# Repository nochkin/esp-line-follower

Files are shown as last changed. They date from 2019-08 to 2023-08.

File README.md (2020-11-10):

# esp-line-follower
## Purpose
The goal of the project is to teach beginners into robotics without fearing and over-complicated or expensive parts.
It's indended to be open enough for future experiments and improvements.

## Required skills
* Basic soldering skills.
  A few wires need to be soldered here and there, nothing major.
* Some understanding on how electronic components are connected together
  Just enough to know the difference between "+" and "-", signal and power lines, etc.
* Basic knowledge on Arduino IDE and how sketches are uploaded.

## Required parts
This is the minimum list of required parts. Basically, these are the parts which are being used in this project.
The list should not limit you in case if you wish to add some additional functionality or make other experiments based on that.
* Microcontroller board.
  The project uses ESP8266 NodeMCU board with CP2102. Sometimes that board is referenced as "ESP8266 NodeMCU v2 DevKit".
  There are some variations of ESP8266 NodeMCU board with CH340G chip, but these are too wide to fit into motor driver shield and so can't be used.
* Motor driver shield.
  The shield is based on L293DD chip. A single chip contains four half-bridges which can be connected as two full bridges to drive two motors.
* A pair of Reflective Infrared sensor boards.
  These are sometimes called "Obstacles avoiding infrared sensor board". Each board contains an infrared LED and infrared photodiode.
  There are a lot of variations of those boards. I highly recommend to pick those with a small adjustment, this way it can be adjusted according to the current lighting and surrounding contrast.
* 2WD Robot Chassis.
  Normally, the chassis comes with two motors with built-in reductors, 4*AA battery holder and enough screws and mounting hardware to put everything together. You will still need some additional mounting/screws to put your ESP8266, Motor shield and Infrared sensors.

## Bill Of Materials (BOM)
All prices are approximate and depend on the source where you purchase it. My recommended sources are eBay and AliExpress. You can also find it on Amazon, but it tends to be slightly more expensive. All prices are in USD.

Qnty | Part | Cost | Buy
-- | - | - | -
1 | ESP8266 NodeMCU (CP2102) | $5.00 | [eBay](https://www.ebay.com/itm/201542946669), [AliExpress](https://www.aliexpress.com/item/32716698412.html), [Amazon](https://www.amazon.com/ESP8266-microcontroller-NodeMCU-WiFi-CP2102/dp/B071WRD25D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)
1 | L293DD Motor Shield for ESP8266 NodeMCU | $2.50 | [eBay](https://www.ebay.com/itm/400999618519), [AliExpress](https://www.aliexpress.com/item/32870926299.html), [Amazon](https://www.amazon.com/BeediY-NodeMCU-ESP-12E-ESP8266-Control/dp/B07QVCMM5B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)
2 | Infrared sensors | $1.50 | [eBay](https://www.ebay.com/itm/132461910910), [AliExpress](https://www.aliexpress.com/item/32757950384.html), [Amazon](https://www.amazon.com/HiLetgo-Infrared-Avoidance-Reflective-Photoelectric/dp/B07W97H2WS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)
1 | 2WD Robot Chassis | $8.00 | [eBay](https://www.ebay.com/itm/253202993406), [AliExpress](https://www.aliexpress.com/item/32766175672.html), [Amazon](https://www.amazon.com/SainSmart-Smart-Chassis-Tracing-Encoder/dp/B07DNYQ3PX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)
6 | 20cm Dupont Wires F-F to connect Infrared boards | $2.00 | [eBay](https://www.ebay.com/itm/283983743599)
1 | Various M3 spacers/standoffs/screws | $12.00 | [eBay](https://www.ebay.com/itm/173901459487), [AliExpress](https://www.aliexpress.com/item/32799855557.html), [Amazon](https://www.amazon.com/Yosoo-120pcs-standoff-motherboard-assortment/dp/B01GO2GWWW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)
1 | Black Cloth Tape, 32mm x 15m | $2.00 | [AliExpress](https://www.aliexpress.com/item/32964092687.html) |

**Total**: about $20

## Connection diagram
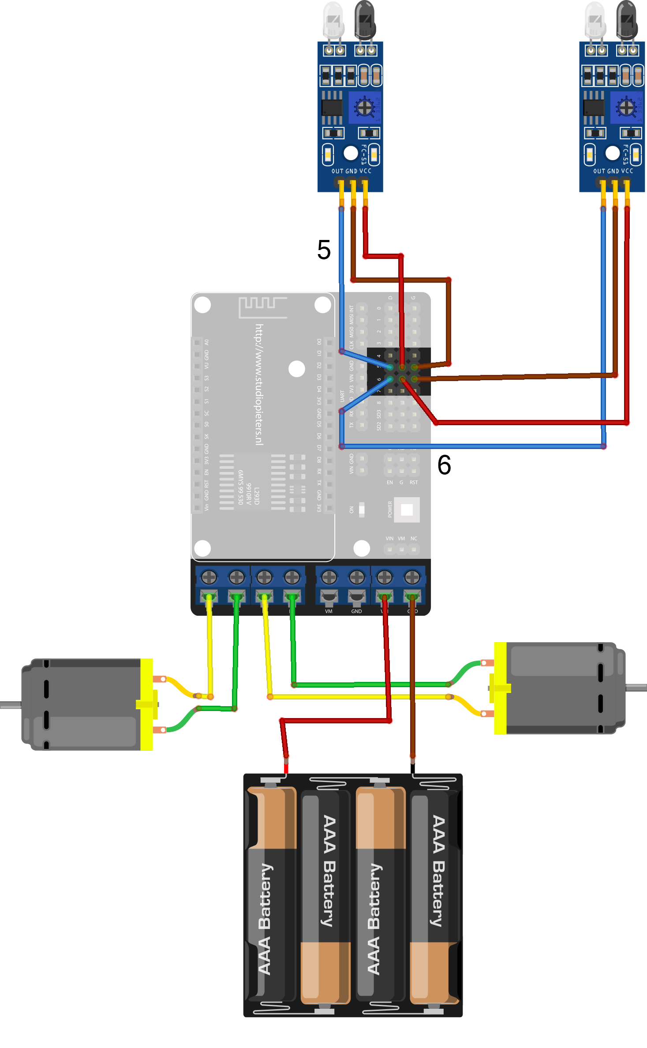
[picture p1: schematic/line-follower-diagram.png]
Fritzing


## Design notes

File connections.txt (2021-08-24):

IR Left:
	14

IR Right:
	12

L293DD DIR Left:
    0

L293DD PWM Left:
    5

L293DD DIR Right:
    2

L293DD PWM Right:
    4

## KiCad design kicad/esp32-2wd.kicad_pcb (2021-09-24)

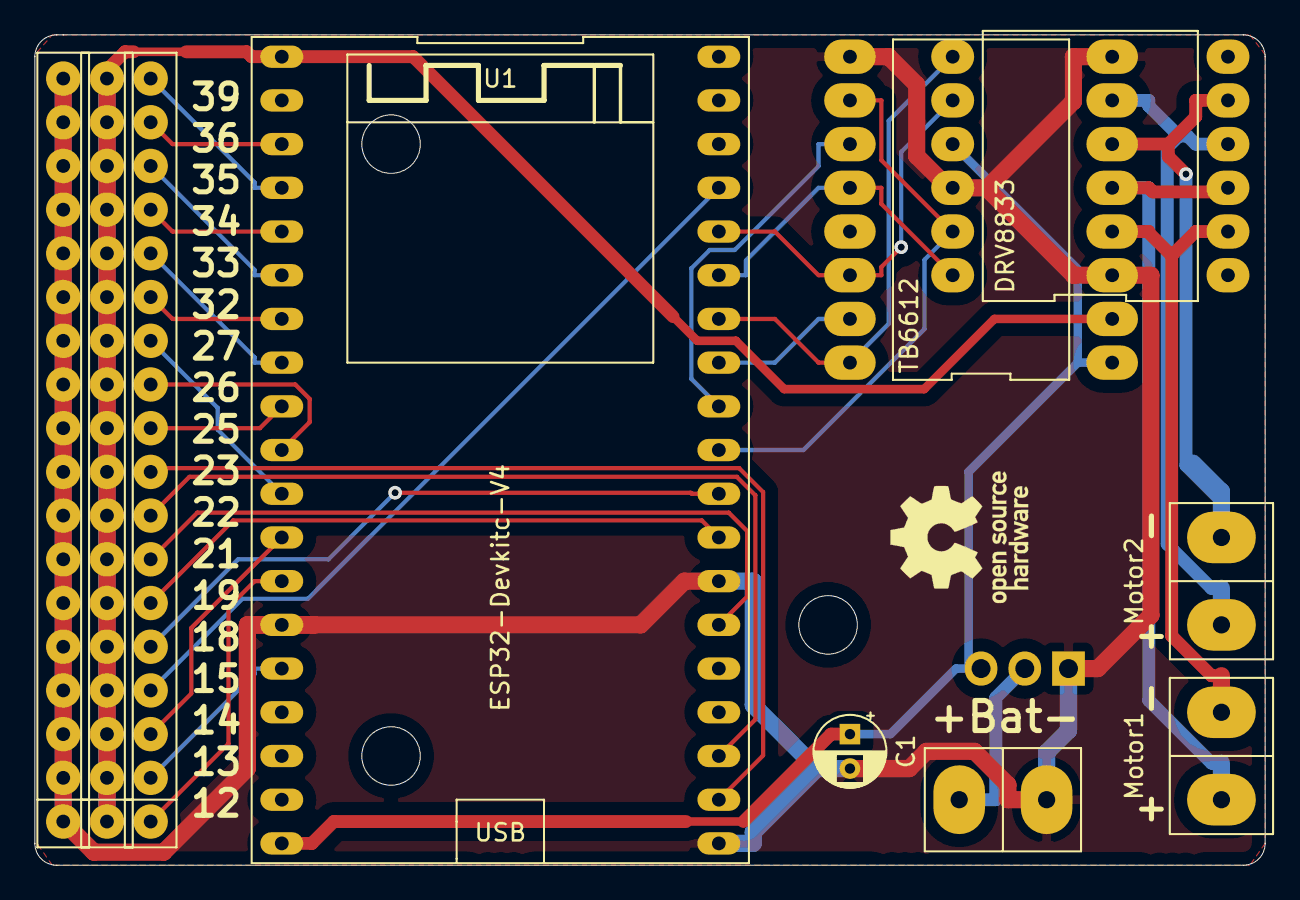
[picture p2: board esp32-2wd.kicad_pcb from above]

Board: 2 copper layers, 71.5 x 48.3 mm, 11 parts (1 on the bottom side), 32 nets.

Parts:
Bat1: Screw_Conn_2p_508
C1: CP; CP_Radial_D4.0mm_P2.00mm
CONN1, CONN2, CONN3: Conn_1x18_254
DRV1: TB6612; TB6612-board
DRV2: DRV8833; DRV8833-12
Motor1, Motor2: Screw_Conn_2p_508
Q1: IRF9540N; TO-220-3_Vertical
U1: ESP32-Devkitc-V4; ESP32-DevKitC-V4-b

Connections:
GNDD: Bat1.1, C1.2, CONN1.1, CONN1.2, CONN1.3, CONN1.4, CONN1.5, CONN1.6, CONN1.7, CONN1.8, CONN1.9, CONN1.10, CONN1.11, CONN1.12, CONN1.13, CONN1.14, CONN1.15, CONN1.16, CONN1.17, CONN1.18, DRV1.3, DRV1.8, DRV1.9, DRV2.10, Q1.1, U1.14, U1.20, U1.26
unnamed: Bat1.2, Q1.2
unnamed: C1.1, DRV1.1, DRV2.9, Q1.3, U1.19
unnamed: CONN2.1, CONN2.2, CONN2.3, CONN2.4, CONN2.5, CONN2.6, CONN2.7, CONN2.8, CONN2.9, CONN2.10, CONN2.11, CONN2.12, CONN2.13, CONN2.14, CONN2.15, CONN2.16, CONN2.17, CONN2.18, DRV1.2, U1.1
unnamed: CONN3.1, U1.13
unnamed: CONN3.2, U1.15
unnamed: CONN3.3, U1.12
unnamed: CONN3.4, U1.35
unnamed: CONN3.5, U1.28
unnamed: CONN3.6, U1.27
unnamed: CONN3.7, U1.25
unnamed: CONN3.8, U1.22
unnamed: CONN3.9, U1.21
unnamed: CONN3.10, U1.9
unnamed: CONN3.11, U1.10
unnamed: CONN3.12, U1.11
unnamed: CONN3.13, U1.7
unnamed: CONN3.14, U1.8
unnamed: CONN3.15, U1.5
unnamed: CONN3.16, U1.6
unnamed: CONN3.17, U1.3
unnamed: CONN3.18, U1.4
unnamed: DRV1.4, DRV2.2, Motor1.2
unnamed: DRV1.5, DRV2.3, Motor1.1
unnamed: DRV1.6, DRV2.5, Motor2.2
unnamed: DRV1.7, DRV2.4, Motor2.1
unnamed: DRV1.10, DRV2.11, U1.29
unnamed: DRV1.11, U1.30
unnamed: DRV1.12, DRV2.12, U1.33
unnamed: DRV1.14, DRV2.8, U1.34
unnamed: DRV1.15, U1.31
unnamed: DRV1.16, DRV2.7, U1.32

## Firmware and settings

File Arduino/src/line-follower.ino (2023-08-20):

#include <Arduino.h>

// Motor driver type (one must be uncommented only)
// #define L293DD
#define TB6612

// Pins configuration
#ifdef ARDUINO_ARCH_ESP32
// Pins configuration for ESP32
#define IR_L 12
#define IR_R 13

#if defined(TB6612)
#define MOTOR_L_PWM 4
#define MOTOR_L_PWM_CH 0
#define MOTOR_L_IN1 2
#define MOTOR_L_IN2 16

#define MOTOR_R_PWM 5
#define MOTOR_R_PWM_CH 2
#define MOTOR_R_IN1 0
#define MOTOR_R_IN2 17

#define MOTORS_ENABLE 32
#else
#error "Selected motor driver not supported on ESP32"
#endif

#define SPEED_MAX 140
#else
// Pins configuration for ESP8266
#define IR_L 14 // D5
#define IR_R 12 // D6

#if defined(L293DD)
#define MOTOR_L_PWM 5 // D1
#define MOTOR_L_DIR 0 // D3
#define MOTOR_R_PWM 4 // D2
#define MOTOR_R_DIR 2 // D4
#else
#error "Selected motor driver not supported on ESP8266"
#endif

#define SPEED_MAX 1023
#endif

class MotorL293DD {
  public:
    MotorL293DD(uint8_t, uint8_t);
    MotorL293DD(uint8_t, uint8_t, bool);
    void forward(uint16_t);
    void reverse(uint16_t);
    void stop();
  protected:
    void set_speed(uint16_t);
    uint8_t pwm_pin, dir_pin;
    bool inv;
};

MotorL293DD::MotorL293DD(uint8_t pwm_pin, uint8_t direction) {
  MotorL293DD(pwm_pin, direction, 0);
}

MotorL293DD::MotorL293DD(uint8_t pwm_pin, uint8_t direction, bool inverse) {
  pwm_pin = pwm_pin;
  dir_pin = direction;
  inv = inverse;
  pinMode(pwm_pin, OUTPUT);
  pinMode(dir_pin, OUTPUT);
  this->stop();
}

void MotorL293DD::set_speed(uint16_t speed) {
  analogWrite(pwm_pin, speed > 1023 ? 1023 : speed);
}

void MotorL293DD::forward(uint16_t speed) {
  digitalWrite(dir_pin, inv ? HIGH : LOW);
  this->set_speed(speed);
}

void MotorL293DD::reverse(uint16_t speed) {
  digitalWrite(dir_pin, inv ? LOW : HIGH);
  this->set_speed(speed);
}

void MotorL293DD::stop() {
  this->set_speed(0);
}

class MotorTB6612 {
  public:
    MotorTB6612(uint8_t, uint8_t, uint8_t, uint8_t);
    MotorTB6612(uint8_t, uint8_t, uint8_t, uint8_t, bool);
    void forward(uint16_t);
    void reverse(uint16_t);
    void stop();
  protected:
    void set_speed(uint16_t);
    uint8_t pwm_pin, pwm_ch, in1_pin, in2_pin;
    bool inv;
};

MotorTB6612::MotorTB6612(uint8_t in_pwm, uint8_t in_pwm_ch, uint8_t in1, uint8_t in2) {
  MotorTB6612(pwm_pin, pwm_ch, in1, in2, 0);
}

MotorTB6612::MotorTB6612(uint8_t in_pwm, uint8_t in_pwm_ch, uint8_t in1, uint8_t in2, bool inverse) {
  pwm_pin = in_pwm;
  pwm_ch = in_pwm_ch;
  in1_pin = in1;
  in2_pin = in2;
  inv = inverse;
  pinMode(in1_pin, OUTPUT);
  pinMode(in2_pin, OUTPUT);
#ifdef ARDUINO_ARCH_ESP32
  ledcSetup(pwm_ch, 5000, 8);
  ledcAttachPin(pwm_pin, pwm_ch);
#endif
  this->stop();
}

void MotorTB6612::set_speed(uint16_t speed) {
#ifdef ARDUINO_ARCH_ESP32
  ledcWrite(pwm_ch, speed > 255 ? 255 : speed);
#else
  analogWrite(pwm_pin, speed > 255 ? 255 : speed);
#endif
}

void MotorTB6612::forward(uint16_t speed) {
  digitalWrite(in1_pin, inv ? HIGH : LOW);
  digitalWrite(in2_pin, inv ? LOW : HIGH);
  this->set_speed(speed);
}

void MotorTB6612::reverse(uint16_t speed) {
  digitalWrite(in1_pin, inv ? LOW : HIGH);
  digitalWrite(in2_pin, inv ? HIGH : LOW);
  this->set_speed(speed);
}

void MotorTB6612::stop() {
  this->set_speed(0);
}

#if defined(L293DD)
MotorL293DD left(MOTOR_L_PWM, MOTOR_L_DIR, false);
MotorL293DD right(MOTOR_R_PWM, MOTOR_R_DIR, true);
#elif defined(TB6612)
MotorTB6612 left(MOTOR_L_PWM, MOTOR_L_PWM_CH, MOTOR_L_IN1, MOTOR_L_IN2, true);
MotorTB6612 right(MOTOR_R_PWM, MOTOR_R_PWM_CH, MOTOR_R_IN1, MOTOR_R_IN2, true);
#else
#error "Selected motor driver not supported"
#endif

void setup() {
  Serial.begin(115200);

  pinMode(IR_L, INPUT);
  pinMode(IR_R, INPUT);

  delay(1000);

  Serial.println("Started");

#ifdef MOTORS_ENABLE
  pinMode(MOTORS_ENABLE, OUTPUT);
  digitalWrite(MOTORS_ENABLE, HIGH);
#endif
}

void loop() {
  uint16_t ir_l = digitalRead(IR_L);
  uint16_t ir_r = digitalRead(IR_R);

  if ((ir_l == LOW) && (ir_r == LOW)) {
    // both sensors are on white
    left.forward(SPEED_MAX);
    right.forward(SPEED_MAX);

  } else if ((ir_l == HIGH) && (ir_r == HIGH)) {
    // both sensors are on black, stop
    left.stop();
    right.stop();

  } else if (ir_l == LOW) {
    // left sensor is on white, right is on the line
    left.forward(SPEED_MAX);
    right.reverse(SPEED_MAX/1.3);
    
  } else if (ir_r == LOW) {
    // right sensor is on white, left is on the line
    left.reverse(SPEED_MAX/1.3);
    right.forward(SPEED_MAX);
  }
}

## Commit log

2019-07-21 Sample Arduino code/library
2019-07-29 Swap left/right motor logic
    [line-follower.ino]
2019-09-17 Add some Amazon links to BOM
2019-09-25 Added missing item to BOM
2021-09-10 ESP32 compatibility
2021-09-24 Add KiCad files for ESP32 board
    [esp32-2wd.kicad_pcb, esp32-2wd.sch]
2021-09-24 Add KiCad's custom lib for ESP32 schematic
2022-08-16 Revert "TB6612 support"
    This reverts commit 02e79df51a6babfc2041ab42208772d88f71af53.
    [line-follower.ino]
2022-08-16 Fix TB6612 support (ESP32 only) and compatibility fixes for ESP8266
    [line-follower.ino]
2022-08-16 Support Enable pin for motor driver, add 1 sec delay before start
2022-08-19 Use ledc instead of pwm for ESP32
